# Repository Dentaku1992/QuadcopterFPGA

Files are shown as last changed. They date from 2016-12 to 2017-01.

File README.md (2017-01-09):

#Design of a quadcopter controller in VHDL

###Overview

In this project, a quad copter flight controller was designed in 'pure' hardware making use of a FPGA (Mojo development board). A PID control unit was used in order to provide stabilization around the three axes of movement of the quad copter. Due to the limited resources that are available on the FPGA (Spartan 6 SLX9), different approaches are used to fit the PID controllers into the FPGA. It was investigated whether there can be made use of the high-speed DSP48 slices available in the Spartan 6 or the Xilinx IP Core multiplier. In order to achieve a minimal resource design, the different channels of the FPGA were multiplexed.

In addition to the design of a PID controller, various other system components were designed as well. 
	
- A PWM generator to control the BLDC engines.
- A mixing unit, to generate the correct control signal for each engine.
- An SPI slave interface to communicate with different sensors and make it possible to access the quadcopter's register.
- A PWM reader in order to read the incomming signal from te remote control.

All hardware was simulated and then tested on an FPGA. Using Matlab and Simulink the necessary calculations and simulations are made before the VHDL implementation was done. In addition to the hardware, the quadcopterframe is fully designed as well. This frame is designed in such a way that it consists of several parts which can be manufactured by a 3D printer.

###Author

Gert-Jan Andries - http://www.gertjanandries.com - info@gertjanandries.com

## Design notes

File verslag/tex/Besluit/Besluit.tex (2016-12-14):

\chapter{Besluit}
\label{besluit}

	\par Het project heeft een zeer grote omvang en kon tijdens de duurtijd van het projectlab niet volledig voltooid worden. Een overzicht van welke items voltooid werden en welke niet, is weergegeven in figuur \ref{quad_ready}.

	\begin{figure}[H]					  
		  \centering
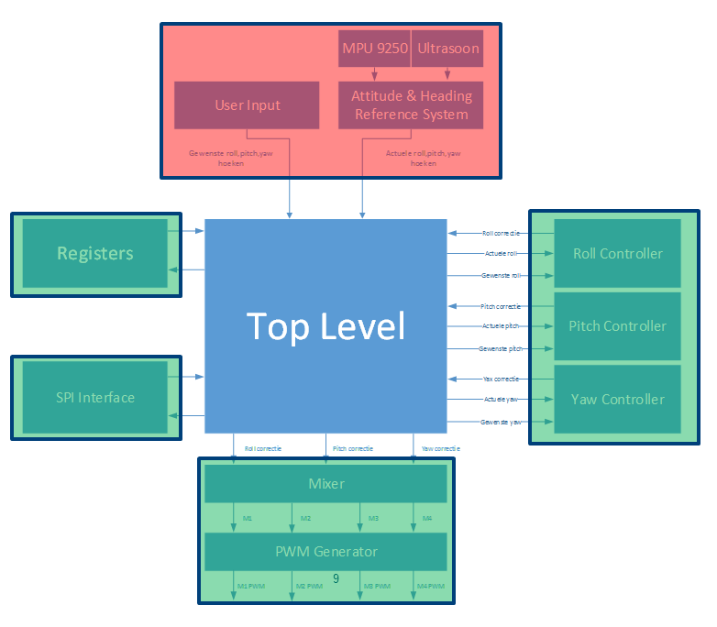
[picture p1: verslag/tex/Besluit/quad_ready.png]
		  
		  \caption{Overzicht van de projectstatus}
		  \label{quad_ready}
	\end{figure}

	\par De PID controller is volledig ge\"implementeerd  en geoptimaliseerd naar resources zodat deze past in de Spartan 6 FPGA. Hierbij werden verschillende iteraties doorlopen die telkens een andere methodiek gebruikten. Aan de hand van Simulink en testbenches werd de werking van de PID controller gevalideerd. De PID controller kon omwille van het ontbreken van sensordata nog niet getest worden op de FPGA zelf. Wel werd al een synthese uitgevoerd om na te gaan of de verschillende PID controllers pasten in het FPGA ontwerp. 

	\par De SPI slave interface werd ontwikkeld aan de hand van dezelfde parameters als het Mojo board gebruikt om te communiceren met de analoge inputs. Op deze manier kan de SPI interface veelzijdig ingezet worden. Via een testbench werd de werking gevalideerd alvorens de interface uit te testen op een FPGA. Wanneer de testbench het gewenste resultaat gaf, werd een test uitgevoerd op de FPGA zelf. Ook hier was de werking perfect en kwamen geen problemen aan het licht.

	\par De PWM generator en motormixer zijn volledig ge\"implementeerd in VHDL. De werking van de PWM generator is reeds getest op een FPGA door het aansturen van de vier verschillende motoren. Hierbij werd ook gebruik gemaakt van de SPI interface om de gewenste PWM instelling te maken. Alles werkt naar behoren. Er dient wel rekening gehouden te worden dat bij het aanleggen van het systeem een vaste PWM waarde aan de motoren wordt aangelegd om deze te activeren. Na ongeveer 1 \'a 2 seconden (beepgeluid bij de motor) zijn de motoren actief en kunnen ze gebruikt worden.

	\par Het quadcopterframe is vollledig geprint, maar dient nog geassambleerd te worden. Door de relatief lange printtijd was er onvoldoende tijd om deze assemblage uit te voeren gedurende het projectlab. De laatste prints waren helaas pas de dag zelf klaar.

	\par Het globale autopilot systeem kon niet getest worden omdat nog niet alle componenten voltooid zijn. De delen die wel getest konden worden, zijn uitvoerig getest en gaven ook het verwachte resultaat.

	\par In het verdere verloop van het project dienen volgende taken nog uitgevoerd te worden.

		\begin{itemize}
			\item Assamblage van het frame.
			\item Alle systeemcomponenten met elkaar verbinden.
			\item Implementeren van AHRS door middel van SPI slave connectie.
			\item Alle data tussen de verschillende componenten in het juiste formaat omzetten.
			\item Bepalen van de K\textsubscript{p}, K\textsubscript{i} en K\textsubscript{d} parameters.
			\item Uitbreiden van de registers.
			\item Globale systeemtest.
		\end{itemize}

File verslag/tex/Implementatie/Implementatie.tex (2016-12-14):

\chapter{Implementatie}

	\par In dit hoofdstuk zal de implementatie van het volledige systeem besproken worden. Er zal vooral de nadruk gelegd worden op de moeilijkheden en problemen die zich voordeden tijdens het ontwikkelproces.

	\section{PID regelaar}

		\par De PID regelaar vormt het belangrijkste onderdeel van de quadcoptersturing. Deze component zal per as ge\"implementeerd moeten worden. Daarnaast kan de PID in een verder stadia ook gebruikt worden om de hoogte te stabiliseren. Er dient dus een flexibele component ontworpen te worden die meerdere malen ingezet kan worden. Hierbij is het belangrijk dat de waarden voor K\textsubscript{p}, K\textsubscript{i} en K\textsubscript{d} per controller ingesteld kunnen worden. Daarnaast is het ook mooi meegenomen om deze real-time aanpasbaar te maken. 

		\par De PID controller werd ontwikkeld in drie iteraties. Vanwege de hardware beperkingen van de FPGA was het nodig om een volledig re-design uit te voeren van de component. Deze stappen zullen hieronder verder toegelicht worden.

		\subsection{PID controller door middel van DSP48A slices}

			\par Vanuit theoretisch oogpunt zijn DSP48 slices ideaal voor het implementeren van een PID regelaar. De bewerkingen die uitgevoerd dienen te worden beperken zich tot optellen en vermenigvuldigen (MAC). Op deze manier wordt een hoge snelheid van de component mogelijk. Per PID regelaar zijn vier DSP48 slices nodig. In figuur \ref{pid_dsp48} is de onderverdeling weergegeven van DSP48 slices binnen de PID regelaar. Hierbij zijn de functies van slice 2 en 3 exact hetzelfde. Bij de laatste DSP48 slice is een terugkoppeling voorzien. Om ervoor te zorgen dat het resultaat nooit overflowt, dient er een downscaling te gebeuren bij de terugkoppeling. Deze wordt in \textquotesingle gewone\textquotesingle   logica uitgevoerd en zal het proces vertragen. Door het introduceren van de nodige \textquotesingle pipes\textquotesingle  wordt de maximale snelheid van implementatie bereikt.
				
				\begin{figure}[H]					  
					  \centering
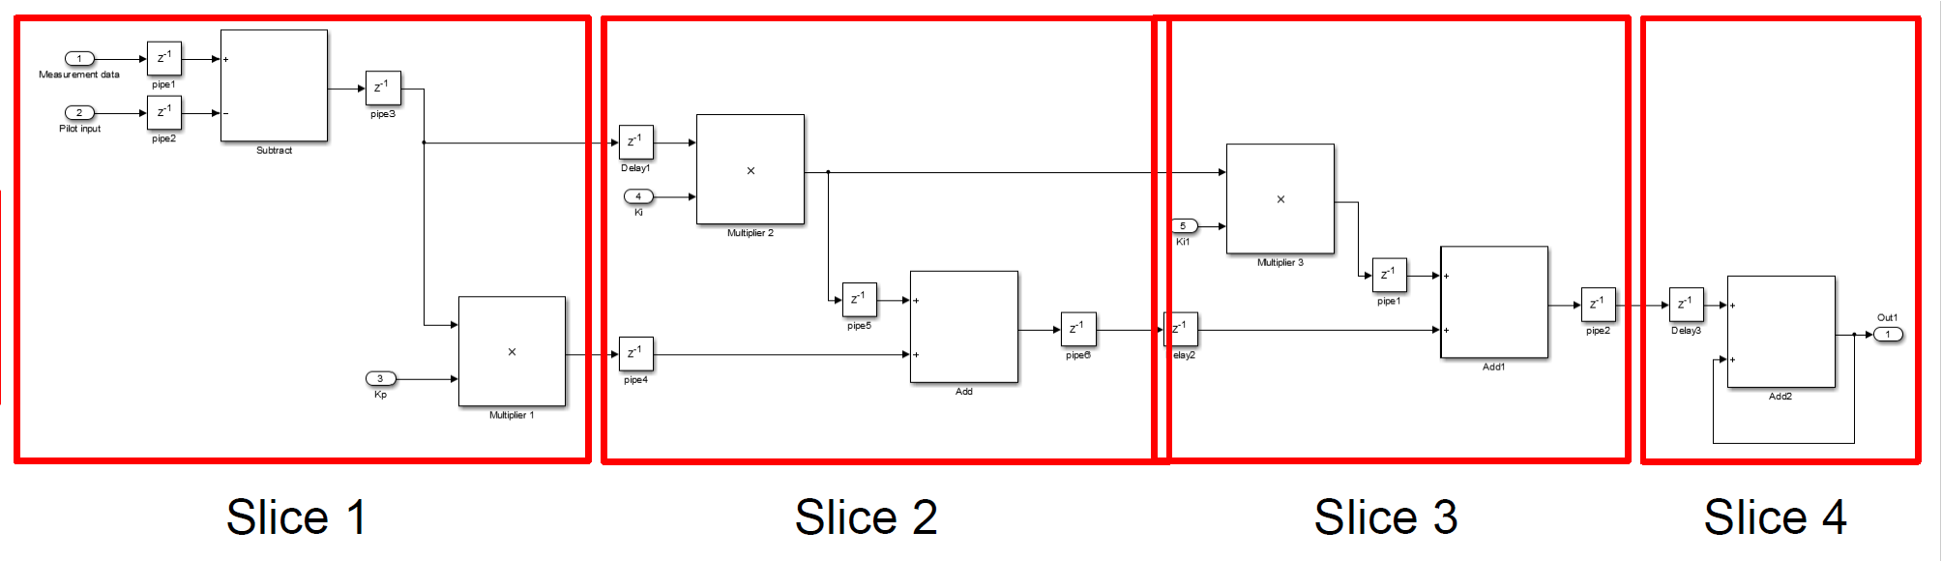
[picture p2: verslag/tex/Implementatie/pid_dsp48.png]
					  
					  \caption{Overzicht van een PID controller op basis van DSP48 slices}
					  \label{pid_dsp48}
				\end{figure}

			\par Bovenstaande code werd in een eerste fase ge\"implementeerd door middel van de Xilinx System Generator. Wanneer de VHDL code gegenereerd diende te worden, doken er steeds fouten op. Opzoekwerk heeft uitgewezen dat de System Generator niet compatibel is met Windows 8. Een Windows 7 apparaat met alle nodige software en licenties was helaas niet beschikbaar. Er werd overgegaan naar het implementeren van de PID in Xilinx ISE. Hierbij werd gebruik gemaakt van de IP Coregen voor het genereren van de juiste instellingen binnen de DSP48 slices.

			\par Door eerste synthese resultaten bleek dat het niet mogelijk was om drie of vier PID's te implementeren op de Spartan 6 FPGA wegens gebrek aan resources. Een mogelijke oplossing was het multiplexen van de PID regeling. Op die manier is er slechts \'e\'en PID regelaar nodig die afwisselend de berekeningen uitvoert voor een bepaald kanaal. De implementatie hiervan bleek echter te complex om te realiseren omdat de PID steeds de vorige resultaten nodig heeft om het volgende te berekenen. Deze data zou dus moeten opgeslagen worden. Daarnaast was het ook niet steeds mogelijk om deze waarden terug op de juiste plaats in het DSP48 slice te laden vanwege de beperkingen van ingangssignalen.

			\par Er dient dus een andere oplossing gevonden te worden om de PID in de Spartan 6 FPGA te implementeren.

		\subsection{PID controller door middel van IPCore multiplier}
		\label{pid_mult}

			\par Een tweede aanpak was om de PID te implementeren aan de hand van \textquotesingle gewone\textquotesingle  logica. Om de vermenigvuldigingen uit te voeren wordt gebruik gemaakt van de IP Core multiplier. Er zijn dus drie van deze multipliers nodig om de volledige component te realiseren. 

			\par Bij het aanmaken van deze multipliers zijn verschillende keuzes mogelijk. Er kan gekozen worden tussen een implementatie die gebruik maakt van ExtremeDSP (DSP48A slices) of een implementatie die gebruik maakt van LUT's en FF. Afhankelijk van de gekozen optie zullen de timings verschillen. Er is ook een mogelijk om te optimaliseren naar area (minimaal gebruik aan resources) of naar snelheid. Er werd gekozen om te minimaliseren naar area. Hierbij maakte de multiplier enkel gebruik van LUT's en FF. 

			\par Via Xilinx Vivado werd een eerste versie van deze PID ge\"implementeerd en gesimuleerd. De keuze voor Vivado werd gemaakt omwille van problemen met de ISE simulator op Windows 8. Daarnaast was het ook niet mogelijk om CoreIP componenten te simuleren in Modelsim vanwege een probleem met de bibliotheken. Xilinx biedt deze niet meer aan, omdat zij een eigen simulator ontwikkeld hebben.

			\par De simulaties leverden dezelfde resultaten op als bekomen in Simulink. Er kon dus besloten worden dat de implementatie van de PID gelijkaardig is als de versie in Simulink. Bij het verder onderzoeken van de synthese resultaten bleek dat er op het eerste zicht voldoende resources beschikbaar waren om vier PID controllers te implementeren. Omdat er niet enkel een PID op de FPGA ge\"implementeerd moet worden, maar ook nog een reeks andere componenten zou het toch kunnen dat men niet voldoende resources ter beschikking heeft.

			\par  Er dient dus een andere oplossing gevonden te worden om de PID in de Spartan 6 FPGA te implementeren met een minimaal gebruik aan resources.

		\subsection{PID controller door middel van multiplexed IPCore multiplier}			

			\par Een oplossing om de resources binnen een PID controller aanzienlijk te beperken is door in plaats van drie multipliers slechts \'e\'en multiplier te gebruiken. Hierbij zal telkens de P, I en D actie uitgevoerd worden. De snelheid van het component zal hierdoor dalen met ongeveer een facor drie, maar dit zal weinig invloed hebben op de werking van de autopilot. Aangezien de sensordata binnenkomt met een snelheid van enkele kHz en de PID component geklokt kan worden aan een snelheid van enkele MHz zal hier geen effect van opgemerkt kunnen worden.

			\par De implementatie gebeurt door middel van een state machine. In een eerste state zullen de  K\textsubscript{p}, K\textsubscript{i} en K\textsubscript{d} waarden ingelezen worden. Op deze manier zijn ze per berekening real-time aanpasbaar. In de volgende states zullen de P, I en D acties uitgevoerd worden. Dit houdt in dat de data die aan de multiplier aangelegd wordt, wijzigt per state. In de laatste state wordt een vlag kort hoog geplaatst om aan te geven dat de berekening klaar is. Er is dus maar \'e\'en multiplier nodig die gemultiplext wordt.

			\par Door het beperken van het aantal multipliers kon de snelheid van de multiplier geoptimaliseerd worden door toch gebruik te maken van DSP48 slices binnen deze multiplier. Deze wijziging werd dan ook doorgevoerd in de component.
\newpage
			\par Simulaties van de bovenstaande PID leverden exact hetzelfde resultaat op als de PID beschreven in paragraaf \ref{pid_mult}. Een overzicht van deze testbench is weergegeven in figuur \ref{pid_tb_mult}.

				\begin{figure}[H]					  
					  \centering
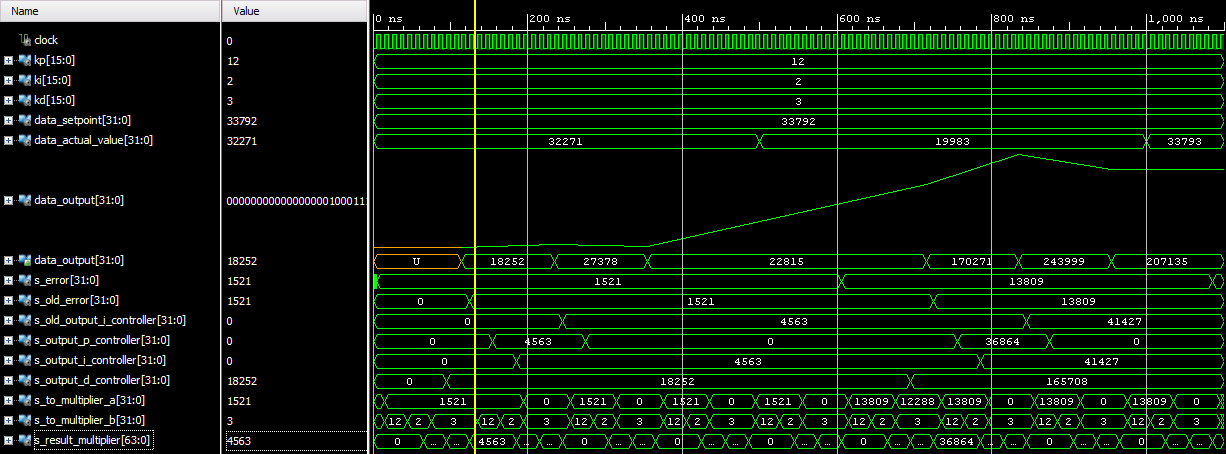
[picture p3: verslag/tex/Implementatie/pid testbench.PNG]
					  
					  \caption{Simulatieresultaat van PID regelaar met gemultiplext multiplier}
					  \label{pid_tb_mult}
				\end{figure}

			\par Wanneer men figuur \ref{pid_tb_mult} nader bekijkt, kan men opmerken dat wanneer de wenswaarde bereikt is, en bijgevolg het errorsignaal 0 is, de uitvoer niet terugvalt naar 0. De reden hiervoor is eenvoudig te verklaren. Aangezien de testbench werkt door middel van het aanleggen van bepaalde signalen voor gemeten waarde op bepaalde tijdstippen, heeft men hier niet te maken met een echt systeem. De I actie van de PID wordt berekend door middel van volgende formule.

				\[ I\textsubscript{regelaar} = (Error \cdot K\textsubscript{i} + Old_K\textsubscript{i} ) \] 

			\par Er wordt dus steeds een berekening gemaakt op basis van de oude waarde van K\textsubscript{i} waardoor de waarde nooit 0 wordt in de simulatie. In een echt systeem wordt dit probleem onmiddellijk opgelost omdat de regelaar zal blijven bijregelen. De sensor zal opmerken dat de waarde de wens overstijgt en een tegenactie ondernemen. 

		\subsection{Samenvattig PID controller}

			\par In listing \ref{PID_list_1} is de componentdefinitie van de PID controller weergegeven. Als invoer zijn zowel de sensordata als de gewenste waarde nodig. Daarnaast moeten ook de co\"effici\"enten voor  K\textsubscript{p}, K\textsubscript{i} en K\textsubscript{d} aangelegd worden. Deze co\"effici\"enten zijn real-time aanpasbaar.
\newpage
			\par Door de PID regelaar in verschillende stappen te ontwerpen konden steeds resources bespaard worden. Dit ging wel steeds ten koste van de snelheid van de component. Hoge snelheid bij deze component is niet zo belangrijk vanwege de relatief trage snelheid weermee de invoerdata kan aangeleverd worden. 

				\lstinputlisting[style=vhdl, caption=Overzicht van de PID component, label=PID_list_1]{Implementatie/pid.vhd}

	\section{PWM generator}

		\par Per motor is er telkens \'e\'en PWM generator nodig bij de quadcopter. De PWM generator zal een PWM signaal genereren op basis van een invoerwaarde die afkomstig is van de motormixing component. Om flexibiliteit te garanderen is de component volledig generiek gemaakt. Op deze manier kan zowel de resolutie als PWM frequentie gewijzigd worden. Een overzicht van de PWM component is weergegeven in listing \ref{pwm_gen}. 

			\lstinputlisting[style=vhdl, caption=Overzicht van de PWM component, label=pwm_gen]{Implementatie/pwm_gen.vhd}

	\section{Motor Mixing}

		\par Het motormixing gedeelte van de quadcopter is verantwoordelijk voor het genereren van de signalen die naar elke motor gestuurd moeten worden. Bij de opbouw van de quadcopter werd gekozen voor de \textquotesingle +\textquotesingle  configuraties. Het mixen van de motors gebeurt dan via het volgend algoritme.

			\[ Motor\textsubscript{front} = baseSnelheid + pitchOutput - yawOutput \]
			\[ Motor\textsubscript{left} = baseSnelheid + rollOutput + yawOutput \]
			\[ Motor\textsubscript{back} = baseSnelheid - pitchOutput - yawOutput \]
			\[ Motor\textsubscript{right} = baseSnelheid - rollOutput + yawOutput \]

		\par Hierbij is de baseSnelheid gelijk aan de idle snelheid van de motor vermeerderd met de throttle.

		\par Net als bij de PWM generator is ook deze component volledig generiek opgebouwd zodat deze makkelijk kan aangepast worden. Een overzicht van deze component is weergegeven in listing \ref{motormixing}.

			\lstinputlisting[style=vhdl, caption=Overzicht van de motormixing component, label=motormixing]{Implementatie/motormixing.vhd}

		\par Er zal ook rekening gehouden worden met de maxima waarde van het systeem. Wanneer een bepaalde waarde het maximum overschrijdt zal deze waarde automatisch worden teruggebracht naar de maximum waarde. De corrigerende actie zal daarom wat minder zijn dan gevraagd, maar de quadcopter blijft op deze manier wel binnen zijn limieten.

	\section{SPI slave interface}

		\par Zoals reeds eerder vermeld werd, voorziet de SPI interface de mogelijkheid om de autopilot te laten communiceren met de buitenwereld. In het vooronderzoek werd reeds de werking van een SPI slave interface aangehaald. Deze is in VHDL ge\"implementeerd voor CPOL en CPHA waarbij beiden gelijk zijn aan 0. Als databreedte werd gekozen voor 8 bits, ofwel 1 byte.

		%\par Via de SPI slave interface is het ook mogelijk om toegang te krijgen tot de analoge pinnen van het Mojo board. Dit kan in het verdere verloop van het project nodig zijn. 

		\par In  listing \ref{spi_slave} is een overzicht weergegeven van het SPI slave component. Er kan data ingevoerd worden die verstuurd moet worden. Daarnaast wordt er ook kort een vlag hoog geplaatst wanneer de data ontvangen is.

			\lstinputlisting[style=vhdl, caption=Overzicht van de SPI slave component, label=spi_slave]{Implementatie/spi_slave.vhd}

		\par Om de werking van deze component te valideren, is er een testbench voor deze component ontworpen. Deze wordt geanalyseerd alvorens de code te testen op het Mojo board. Het resultaat van deze testbench is weergegeven in figuur \ref{spi_slave_tb}.

				\begin{figure}[H]					  
					  \centering
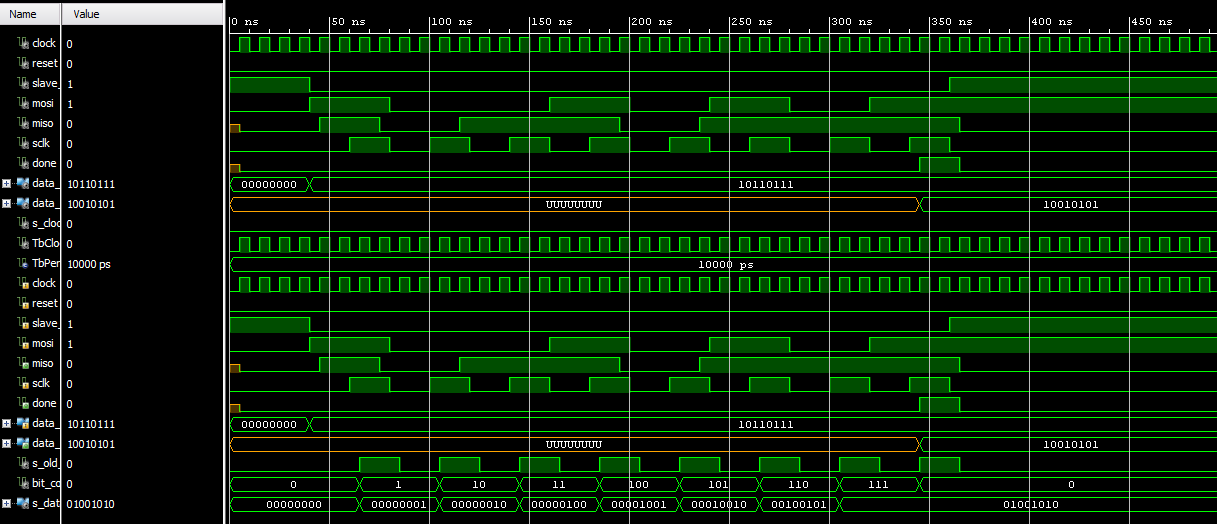
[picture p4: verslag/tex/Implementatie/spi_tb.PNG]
					  
					  \caption{Simulatieresultaat van SPI slave interface}
					  \label{spi_slave_tb}
				\end{figure}

	\section{Top level}

		\par Het toplevel verbindt alle systeemcomponenten met elkaar. Daarnaast is ook op dit niveau de register ge\"implementeerd aan de hand van de IP Coregen. Er wordt gebruik gemaakt van een block memory met 255 registers die elk een grootte hebben van 1 byte. Via de SPI interface kunnen deze registers zowel gelezen als ingesteld worden.

		\par Het toplevel zal ook de nodige signalen naar de buitenwereld brengen. Zo worden de signalen naar de motoren, SPI-apparaten en sensoren naar buiten gebracht. 

		\par Via de IP Core clocking wizard worden de verschillende klokken aangemaakt waarmee de componenten werken. 

	\section{Quadcopter Frame}

		\par Niet alleen de hardware componenten werden ontwikkeld tijdens dit projectlab, ook de quadcopter zelf werd ontworpen. Hierbij wordt gebruik gemaakt van een 3D printer die de verschillende onderdelen zal vervaardigen. In het computerprogramma Inventor worden alle onderdelen getekend en klaargemaakt om te kunnen worden geprint.

		\par Een quadcopter is opgebouwd uit vier armen die gepositioneerd zijn in een \textquotesingle x\textquotesingle. Zo\textquotesingle n arm is weergegeven in figuur \ref{quad_frame_pict}. 

			\begin{figure}[H]					  
				  \centering
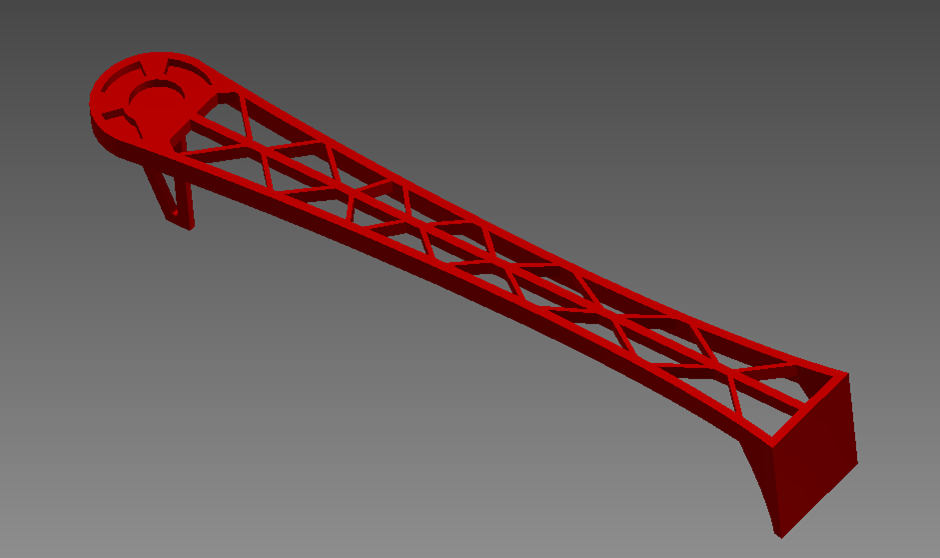
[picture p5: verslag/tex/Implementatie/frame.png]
				  
				  \caption{Weergave van een quadcopter arm}
				  \label{quad_frame_pict}
			\end{figure}

		\par De frameonderdelen werden vervaardigd door middel van een Ultimaker 3D printer. Indien er tijdens de vlucht een bepaald onderdeel beschadigd raakt, kan dit makkelijk opnieuw geprint worden en is quadcopter snel weer operatief. Het printen van een arm neemt ongeveer 4 uur in beslag.

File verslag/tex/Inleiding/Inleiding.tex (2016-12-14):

\chapter{Inleiding}
	
	\par In dit verslag worden de resultaten van het projectlab toegelicht. Elke stap die werd genomen om het eindresultaat te bekomen wordt kort besproken, alsook de moeilijkheden die zich hebben voorgedaan tijdens de ontwikkeling. Tenslotte wordt ook een besluit gevormd over het gehele project en worden de toekomstmogelijkheden kort toegelicht. 

	\section{Omschrijving van de opdracht}

		\par Het project is onderverdeeld in twee grote onderdelen. Enerzijds is er het stabilisatiealgoritme voor de quadcopter en anderzijds is er de sturing, hardware design en optical flowintegratie. De focus van het project zal gelegd worden op de stabiliteitsnelheid van het eindresultaat. Het onderdeel met het stabilisatie-algoritme omvat het genereren van PWM signalen die de motoren aansturen. Hiervoor is sensordata nodig van bijvoorbeeld een gyroscoop, accelerometer, magnetometer en barometer. Om de ruis uit deze metingen weg te filteren zal gebruik gemaakt worden van een filter, bijvoorbeeld Kalman, die ook in de FPGA zal ge\"integreerd worden. Naast data van sensoren zal de FPGA ook informatie ontvangen van een extra processor. Op deze extra processor wordt de communicatie met de grond voorzien (besturing), alsook een optical flow algoritme. 

		\par De stabilisatie zelf zal uitgevoerd worden door een PID of SM (sliding mode) dat ook op de FPGA zal ge\"integreerd worden. De instellingen van het stabilisatie-algoritme zullen gemaakt worden door middel van registers die door de externe processor kunnen ingesteld worden via I\textsuperscript{2}C of SPI. Via deze registers kan ook de actuele sensor- en systeeminformatie opgevraagd worden. De hardware bestaat uit een zelf te ontwikkelen printplaat gebaseerd op een FPGA (Spartan 6) die de stabilisatie en verwerking van de inputs verzorgt. Daarnaast bevat het ook een microcontroller die de communicatie voorziet, alsook de beeldverwerking voor de optical flow en het batterijbeheer. De communicatie zou verlopen volgens het MAVLink protocol, een gestandaardiseerd protocol dat communicatie voorziet onafhankelijk van de fysische laag waarop dit gebeurt. Een keuze voor het beste kanaal maakt ook deel uit van dit project. 
\newpage
		\par Optical flow detectie voorziet de  mogelijkheid om de horizontale ongewenste bewegingen tegen te werken en dus de quadcopter op een vaste positie te houden. De sturing voor de BLDC motoren wordt zelf ge\"implementeerd en vindt plaats op externe processoren die elk instaan voor \'e\'en enkele motor. Het FPGA ontwikkelbord waarmee gewerkt zal worden is het Mojo bord met een Spartan 6 processor. Dit bord zal zelf aangekocht worden. Verder zal ook een MPU9250 gebruikt worden om accelero-, magneto- en gyro-data te verzamelen. De andere sensoren die gebruikt zullen worden dienen te worden bepaald tijdens de looptijd van het project. 

		\par Wanneer alle sensoren getest zijn, worden ze samen met de FPGA (niet het ontwikkelbord) op de zelf ontworpen printplaat geplaatst om zo een quadcoptersturing te verkrijgen die onafhankelijk is van een ontwikkelbord of opgelegde pinout. Deze wordt gemonteerd op de quadcopter structuur die gemaakt zal worden door middel van een 3D printer. Dit maakt het nadien ook mogelijk om bij een crash een bepaald onderdeel snel te reproduceren.

		\par Dit projectlab kan worden opgesplitst in verschillende milestones.
			
		\begin{itemize}
			\item  Stabilisatie en sturing (Gert-Jan)
				\begin{itemize}
					\item Uitlezen sensoren
					\item Uitfilteren van ruis op sensordata
					\item Stabilisatie-algoritme PID/SM
					\item Instellingsmogelijkheid van registers
					\item Ontwerp van quadcopterframe
				\end{itemize}
			\item  Hardware en optical flow (Nick)
				\begin{itemize}
					\item Ontwerpen printplaat
					\item Implementeren MAVLink
					\item Selecteren communicatiekanaal
					\item Optical flow
					\item BLDC motor sturing
					\item Return to home functie
				\end{itemize}
		\end{itemize}
\newpage
	\section{Planning en werkwijze}

		\par De algemene werkwijze van het project kan onderverdeeld worden in vier grote blokken.

			\begin{description}
				
				\item[Onderzoek:] In deze fase van het project wordt een onderzoek uitgevoerd met betrekking tot quadcopters. Er wordt gekeken naar hoe een quadcopter bestuurd wordt en via welke algoritmen dit kan gebeuren. Daarnaast zal ook een studie gemaakt worden naar het implementeren van een PID-controller in een FPGA. Via simulaties in het programma simulink kunnen de algoritmen ge\"evalueerd worden.

				\item[Implementatie:] In deze fase worden de onderzoeksresultaten omgezet in code. Via het programma Xilinx ISE en Vivado wordt de implementatie voorzien op een FPGA. Aan de hand van het programma Modelsim worden de hardwaredesigns ge\"evalueerd alvorens deze op de FPGA worden getest.

				\item[Testen:] Wanneer de hardware gevalideerd is door middel van een testbench, kan deze getest worden op de FPGA zelf. Blok per blok zullen de nodige testen uitgevoerd worden en bijgestuurd waar nodig. 

				\item[Reflectie:] Elk ontworpen blok zal onderworpen worden aan een kritische evaluatie. Hierbij wordt gekeken naar performantie, accuraatheid en werking binnen het geheel. Waar nodig wordt bijgestuurd. Regelmatige communicatie met medestudent Nick, die de hardware (PCB) ontwerpt is hierbij nodig.

			\end{description}

		\par Een beknopte projectplanning wordt hieronder weergegeven. Een uitgebreide versie hiervan is terug te vinden in appendix \ref{app:A} op pagina \pageref{app:A}. Deze uitgebreide versie houdt rekening met de initi\"ele planning. Hieronder is het werkelijke verloop van het project weergegeven.

			\begin{itemize}
				
				\item[Week 1:] 
					\begin{itemize}
						\item Keuze maken van het project uit de aangeboden projecten.  
						\item Registreren van het gekozen project.
					\end{itemize}

				\item[Week 2:] 
					\begin{itemize}
						\item Indienen van de projectplanning.
						\item Onderzoek naar quadcopters en besturing.
						\item Studie PID en digitalisering.
						\item Studie IMU sensoren.
					\end{itemize}

				\item[Week 3:]
					\begin{itemize}
						\item Simulatie van PID algoritme in Matlab en Simulink.
						\item Theoretisch ontwerp van PID door middel van DSP48 slices.
						\item Kennismaking Mojo ontwikelbord en Xilinx ISE.
					\end{itemize}				

				\item[Week 4:]
					\begin{itemize}
						\item Tussentijdse presentatie van het project.
						\item Implementatie van PID door middel van DSP48 slices .
						\item Evaluatie van PID implementatie en bijsturing.
						\item Ontwerp van quadcopter frame in Inventor.
					\end{itemize}					

				\item[Week 5:]
					\begin{itemize}
						\item Ontwerp SPI slave interface in VHDL.
						\item Bijsturen PID ontwerp, implementatie met behulp van IP core multiplier.
						\item Validatie van ontwerp door middel van testbenches.

					\end{itemize}					

				\item[Week 6:]
					\begin{itemize}
						\item Bijsturen PID ontwerp, implementatie met behulp van IP core multiplier.
						\item Validatie van ontwerp door middel van testbenches.
						\item Ontwerp SPI slave interface aanpassen aan Mojo SPI.
						\item Testprint van quadcopter arm en stevigheidstest.
					\end{itemize}					

				\item[Week 7:]
					\begin{itemize}
						\item Bijsturen ontwerp van quadcopter arm.
						\item Printen van vier quadcopterarmen.
						\item Ontwerp van PWM generator in VHDL.
					\end{itemize}					

				\item[Week 8:]
					\begin{itemize}
						\item Tussentijdse presentatie van het project.
						\item Testen PWM generator op Mojo. 
						\item Testen van SPI slave interface op Mojo. 
						\item Ontwerp bijsturen waar nodig.
					\end{itemize}					

				\item[Week 9:]
					\begin{itemize}
						\item PID regeling aanpassen naar multiplexing om resources te besparen op de FPGA.
						\item Valideren van het nieuwe PID ontwerp.
						\item Testen van PWM en SPI samen op Mojo bord.
					\end{itemize}					

				\item[Week 10:]
					\begin{itemize}
						\item Ontwerpen van motormixingalgoritme in VHDL.
						\item Optimalisatie van PID controller.
						\item Implementatie van registers.
					\end{itemize}					

				\item[Week 11:]
					\begin{itemize}
						\item Labobad Gent.
					\end{itemize}					

				\item[Week 12:]
					\begin{itemize}
						\item Eindpresentatie en demo van het labproject.
					\end{itemize}								

				\item[Week 14:]
					\begin{itemize}
						\item Indienen van het eindverslag.
					\end{itemize}

			\end{itemize}

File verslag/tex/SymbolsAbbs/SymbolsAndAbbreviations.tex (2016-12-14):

% Een lijst van figuren en tabellen is optioneel
%\listoffigures
%\listoftables
% Bij een beperkt aantal figuren en tabellen gebruik je liever het volgende:
\listoffiguresandtables
% De lijst van symbolen is eveneens optioneel.
% Deze lijst moet wel manueel aangemaakt worden, bv. als volgt:
\chapter{Lijst van afkortingen}

\begin{flushleft}
  \renewcommand{\arraystretch}{1.1}
  \begin{tabularx}{\textwidth}{@{}p{12mm}X@{}}
			ADC 					& Analog to Digital Converter\\
			ARM 					& Advanced RISC Machines\\			
			AHRS					& Attitude and Heading Reference System\\
			BLDC					& Brushless DC\\
			CPHA					& Phase Polarity\\
			CPOL					& Clock Polarity\\
			DC						& Direct Current \\
			DMP						& Digital Motion Processing\\
			DSP 					& Digital Signal Processing\\		
			ESC						& Engine Speed Controller\\
			FPGA					& Field Programmable Gate Array 	\\
			I\textsuperscript{2}C 	& Inter-IC bus\\		
			IC 						& Integrated circuit\\		
			IMU						& Inertial Measurement Unit\\
			IO						& Input Output\\
			IP						& Intellectual Property\\
			KU 						& Katholieke Universiteit\\		
			KUL 					& Katholieke Universiteit Leuven\\		
			MAC 					& Multiply and Accumulate\\		
			MAVLink					& Micro Air Vehicle Communication Protocol	\\
			MHz 					& Megahertz\\		
			MISO					& Master In Slave Out\\
			MOSI					& Master Out Slave In\\
			PCB 					& Printed Circuit Board\\		
			PID						& Proportioneel Integrerend Differenti\"erend	\\
			PWM						& Pulse Width Modulation\\
			RF						& Radio Frequency\\
			SCLK					& Serial Clock Line\\
			SM						& Sliding Mode	\\
			SPI 					& Serial Peripheral Interface\\		
			SS 						& Slave Select\\
			UART 					& Universal Asynchronous Receiver Transmitter\\		
			USB						& Universal Serial Bus\\		
			VHDL					& Very High Speed Integrated Circuit Hardware Description Language\\

  \end{tabularx}
\end{flushleft}

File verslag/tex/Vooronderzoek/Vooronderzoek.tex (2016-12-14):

\chapter{Vooronderzoek}

	\par In dit hoofdstuk zullen de verschillende resultaten van het vooronderzoek besproken worden. Ook de simulaties in het programma simulink worden kort toegelicht. Op het einde van dit hoofdstuk wordt een compleet systeemoverzicht weergegeven. 

	\section{Quadcopters}

		\subsection{Wat is een quadcopter}
			
			\par Een quadcopter, ook wel quadrocopter genoemd, is een hefschroefvliegtuig dat, zoals de naam al doet vermoeden, aangedreven wordt door vier motoren. In tegenstelling tot een conventionele helikopter maakt een quadcopter gebruik van symmetrisch hellende propellors die in groepen van twee dezelfde draairichting hebben. Op deze manier wordt de tolbeweging die ontstaat door de krachtwerking van de motoren tegengewerkt en gereduceerd tot nul. Dit zorgt ervoor dat de quadcopter tijdens de vlucht niet rondtolt. Bij een klassieke helikopter wordt het opheffen van deze kracht voorzien door de staartrotor.

				\begin{figure}[H]					  
					  \centering
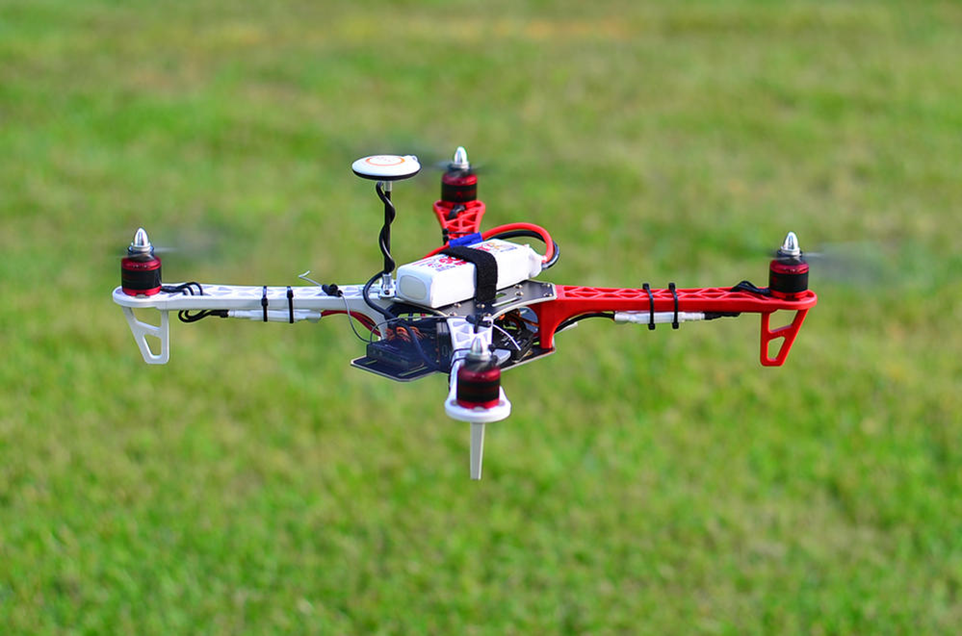
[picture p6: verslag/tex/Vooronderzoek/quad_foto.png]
					  
					  \caption{Quadcopter in actie}
					  \label{quadcopter_foto}
				\end{figure}

			\par Een quadcopter is opgebouwd uit een frame dat vier armen bevat. Op het uiteinde van deze armen zijn de motoren (brushless DC) bevestigd. Om de motoren aan te sturen wordt gebruik gemaakt van een \textquoteleft engine speed controller \textquoteright (ESC). Deze zorgt voor de aansturing van de motoren. Een centrale eenheid regelt zowel de stabilisatie als de invoer van de piloot.

			\par Een quadcopter is van nature onstabiel. Een regelsysteem dat stabilisatie voorziet tijdens de vlucht is nodig. Dit systeem zal ten minste een stabilisatie voorzien rond de roll-, pitch- en yaw-as. Optioneel kan ook een stabilisatie voor drift en hoogte voorzien worden. Deze stabilisatie wordt meestal voorzien door middel van een PID controller voor elke as.

			\par Naast het voorzien van stabilisatie dient er ook gereageerd te worden op de invoer van de piloot. De centrale eenheid (autopilot) implementeert typisch deze functies. Naast het voorzien van deze basisfuncties kunnen nog verschillende opties toegevoegd worden zoals een return-to-home functie, een autoland functie\ldots 

			\par Als basis voor deze autopilot wordt een IMU unit voorzien. Deze beschikt aan de hand van een accelerometer-, magnetometer- en gyroscoop-informatie over de actuele attitude van de quadcopter. Op basis van deze gegevens kan een stabilisatie uitgevoerd worden.

			\par Hiervoor zijn reeds verschillende systemen op de markt. Een populair systeem binnen de amateurpiloten is ArduPilot. Deze autopilot is volledig gebaseerd op Arduino en compatibel met zowat alle quadcopters en kleine vliegtuigen. 

			\par Net zoals ArduPilot zijn zowat alle autopilot systemen momenteel op de markt, gebaseerd op een microcontroller. Het doel van dit projectlab is het onderzoeken of de basisfuncties van een autopilot ook ge\"implementeerd kunnen worden op een FPGA.

		\subsection{Configuraties}

			\par Een quadcopter kan opgebouwd worden op twee verschillende manieren. Afhankelijk van hoe de armen aan het centrale stuk geplaatst worden, verkrijgt men ofwel een \textquoteleft+\textquoteright  ofwel een \textquoteleft x\textquoteright  configuratie. De configuratie wordt dus bepaald door de vliegrichting van de quadcopter ten opzichte van de propellers. In figuur \ref{quad_config} is een overzicht van beide configuraties weergegeven.

				\begin{figure}[H]					  
					  \centering
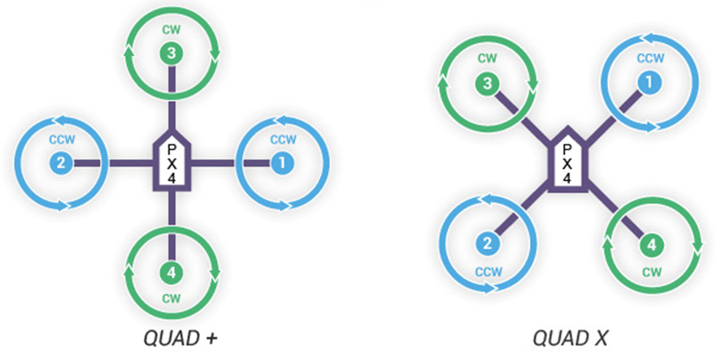
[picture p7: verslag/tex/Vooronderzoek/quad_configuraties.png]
					  
					  \caption{Verschillende configuratiemogelijkheden van een quadcopter}
					  \label{quad_config}
				\end{figure}

			\par De keuze van een bepaalde configuratie heeft een invloed op de manier van besturing, maar ook op het algoritme waarmee de verschillende motoren worden aangestuurd. Wanneer men gebruikt maakt van de  \textquoteleft x\textquoteright configuratie, zijn er twee motoren nodig om een beweging om een bepaalde as uit te voeren. 

			\par Het spreekt voor zich dat het algoritme dat nodig is om de motoren aan te sturen bij een  \textquoteleft x\textquoteright configuratie complexer is dan bij de keuze van een  \textquoteleft +\textquoteright configuratie. Er wordt dus gekozen voor de  \textquoteleft +\textquoteright configuratie binnen dit projectlab.

		\subsection{Besturing van een quadcopter}
			
			\par Om een quadcopter te besturen dienen de motoren op een correcte wijze aangestuurd te worden. Afhankelijk van hoe de motoren aangestuurd worden zal de quadcopter stijgen, dalen, gieren, of stampen. Daarnaast is het ook mogelijk een combinatie van de verschillende bewegingen samen uit te voeren.

			\par Om een quadcopter te laten stijgen of dalen, dienen de vier motoren gelijktijdig versneld of vertraagd te worden. 

			\par Om een quadcopter te laten bewegen om zijn verticale as moet de snelheid van twee motoren die \'e\'enzelfde draairichting hebben verhoogd worden. Hierdoor zal het koppel op de quadcopter toenemen waardoor een gierbeweging zal ontstaan.

			\par Om een quadcopter vooruit, achteruit, link of rechts te laten bewegen in de \textquoteleft + \textquoteright  configuratie volstaat het om \'e\'en motor sneller te laten bewegen dan de anderen. Hierdoor zal de quadcopter kantelen in een bepaalde richting, met een verplaatsing tot gevolg.

			\par In figuren \ref{quad_up_down}, \ref{quad_gieren} en \ref{quad_kantelen} is een overzicht weergegeven van de besturing van een quadcopter in de \textquoteleft + \textquoteright configuratie.

		\begin{figure}[H]
			\centering
				\begin{minipage}[b]{0.3\textwidth}
					\centering
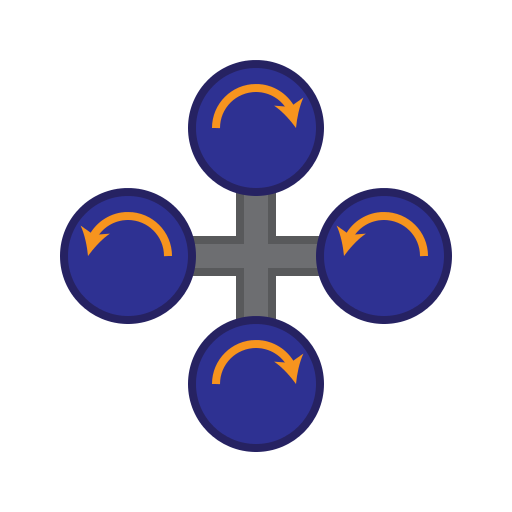
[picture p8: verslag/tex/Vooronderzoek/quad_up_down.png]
					
					\caption[Omhoog en omlaag]{Omhoog en omlaag}
					\label{quad_up_down}
				\end{minipage}
			\quad
				\begin{minipage}[b]{0.3\textwidth}
					\centering
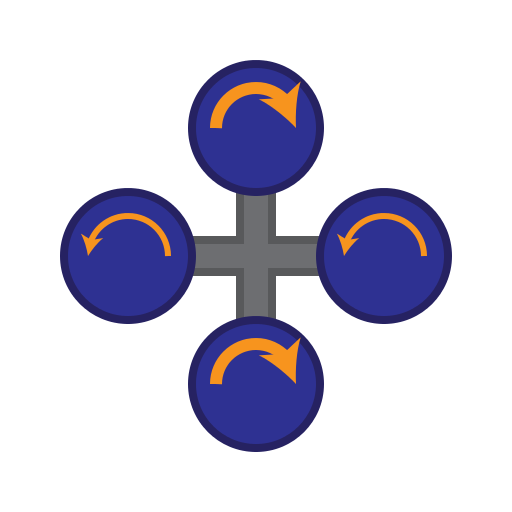
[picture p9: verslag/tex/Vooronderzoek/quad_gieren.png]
					
					\caption[Gieren]{Gieren \newline \ }
					\label{quad_gieren}
				\end{minipage}
			\quad
				\begin{minipage}[b]{0.3\textwidth}
					\centering
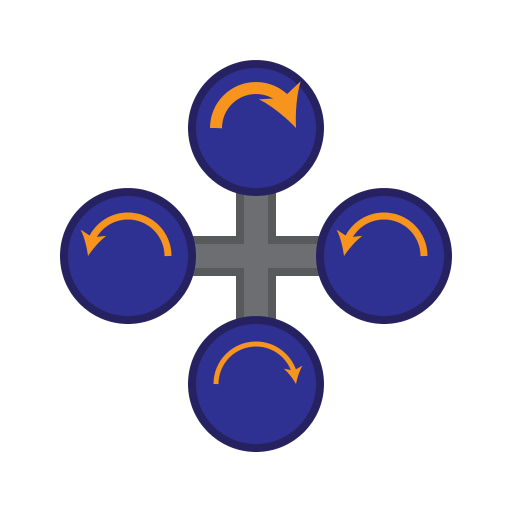
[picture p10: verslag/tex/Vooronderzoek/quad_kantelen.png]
					
					\caption[Kantelen]{Kantelen \newline \ }
					\label{quad_kantelen}
				\end{minipage}
		\end{figure}

	\section{PID regelaar}

		\par Een PID regelaar is een veel voorkomende regelaar binnen de procesregeling. De afkorting PID staat voor Proportioneel, Integrerend en Differenti\"erend. Dit zijn ook de acties waaruit de regelaar is opgebouwd.

		\subsection{Werkingsprincipe}

			\par De regeling gaat uit van het verschil tussen de gewenste waarde en de actuele gemeten waarde. Dit wordt omschreven als het foutsignaal. Het bijsturen van dit foutsignaal gebeurt in drie parallelle stappen.

				\begin{description}
					
					\item[P-actie:] De proportionele actie zal het foutsignaal versterken met een factor K\textsubscript{p}.

					\item[I-actie:] De integrerende actie zorgt voor een constante sommatie van het foutsignaal. Afhankelijk van hoe lang er een fout is tussen de gemeten en gewenste waarde, zal de integrerende actie meer of minder signaal uitsturen. De K\textsubscript{i} term, ook wel nasteltijd genoemd, bepaald het effect van deze actie. Hoe kleiner deze waarde, hoe krachtiger de actie.

					\item[D-actie:] De differenti\"erende actie zal reageren op de snelheid van verandering van het foutsignaal. Hoe hoger de factor K\textsubscript{d} wordt ingesteld, hoe sneller de wenswaarde bereikt zal worden.

				\end{description}

			\par Wiskundig kan men een PID regelaar als volgt omschrijven:

				\[ u(t) = K_{p}\cdot (e(t)+\frac{\int e(t)dt }{T_{i}}+ T_{d}\cdot \frac{de(t))}{dt}) \]

			\par Hierin is 

				\begin{conditions*}
					U(t)				& De uitgang van de regelaar				\\
					K\textsubscript{p}	& De proportionele actie van de regelaar	\\
					T\textsubscript{i}	& De integratietijd van de regelaar			\\
					T\textsubscript{d}	& De differentiatietijd van de regelaar 	\\
					E(t)				& Het errorsignaal							\\
				\end{conditions*}

			\par Het bepalen van de juiste constanten is een werk van trial-and-error. Dit zal dan ook experimenteel moeten vastgesteld worden op de quadcopter.

		\subsection{Digitalisatie van een PID}

			\par De formule die hierboven weergegeven is, kan als volgt vertaald worden naar een digitaal systeem.

				\[ U\textsubscript{k} = U\textsubscript{k-1} \cdot e\textsubscript{k} + b\textsubscript{0} \cdot + b\textsubscript{1} \cdot e\textsubscript{(k-1)} + b\textsubscript{2} \cdot e\textsubscript{(k-2)} \]

			\par Hierbij is

				\begin{itemize}
					\item[] $ b\textsubscript{0} = K\textsubscript{p}(1+ \frac{T\textsubscript{d}}{T}) $ \\					
					\item[] $ b\textsubscript{1} = K\textsubscript{i}(-1 +  \frac{T}{T\textsubscript{i}} -2\frac{T\textsubscript{d}}{T} ) $ \\		
					\item[] $ b\textsubscript{2} = K\textsubscript{d}(\frac{T\textsubscript{d}}{T}) $ \\
				\end{itemize}

			\par Deze formule kan weergegeven worden in het onderstaande schema.
	
				\begin{figure}[H]					  
					  \centering
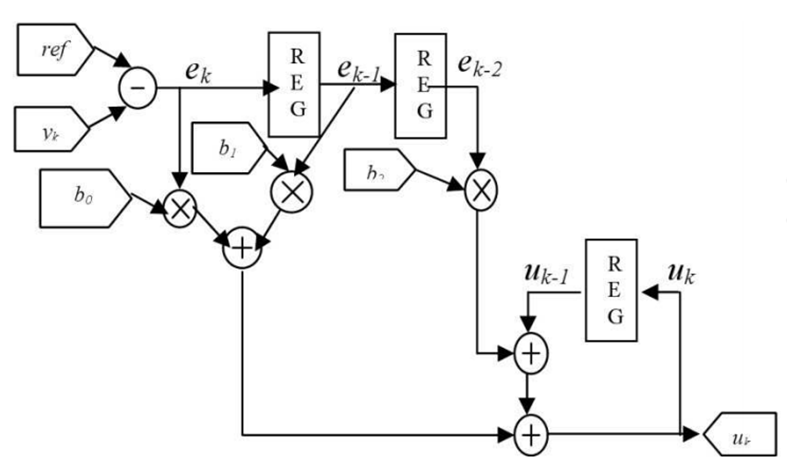
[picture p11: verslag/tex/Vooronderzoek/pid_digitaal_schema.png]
					  
					  \caption{Schematische voorstelling van een PID regelaar}
					  \label{pdi_digitaal_schema}
				\end{figure}

			\par De werking van de in figuur \ref{pdi_digitaal_schema} weergegeven regelaar wordt gevalideerd via het programma Simulink. Op deze manier kan reeds voor de FPGA implementatie gekeken worden of de regelaar zal doen wat er verwacht wordt. Daarnaast vormt deze simulatie een goede basis om het FPGA design te starten. In figuur \ref{pdi_simulink_schema} is de Simulink versie van de PID regelaar weergegeven.

				\begin{figure}[H]					  
					  \centering
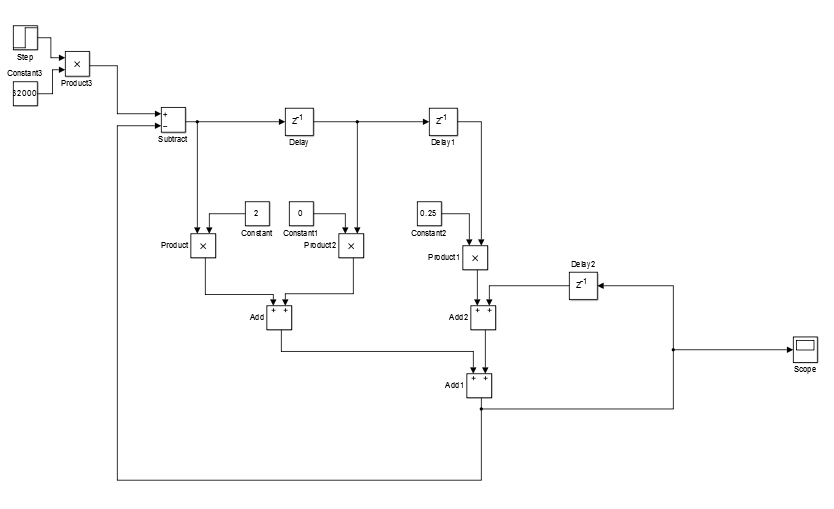
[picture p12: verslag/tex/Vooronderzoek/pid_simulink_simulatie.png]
					  
					  \caption{Simulink voorstelling van een PID regelaar}
					  \label{pdi_simulink_schema}
				\end{figure}

			\par Wanneer men de uitgang aan de ingang koppelt van bovenstaande PID wordt er aangenomen dat de nieuwe gemeten waarde gelijk is aan de uitgang van de PID. Dit levert het volgend resultaat op na simulatie.

				\begin{figure}[H]					  
					  \centering
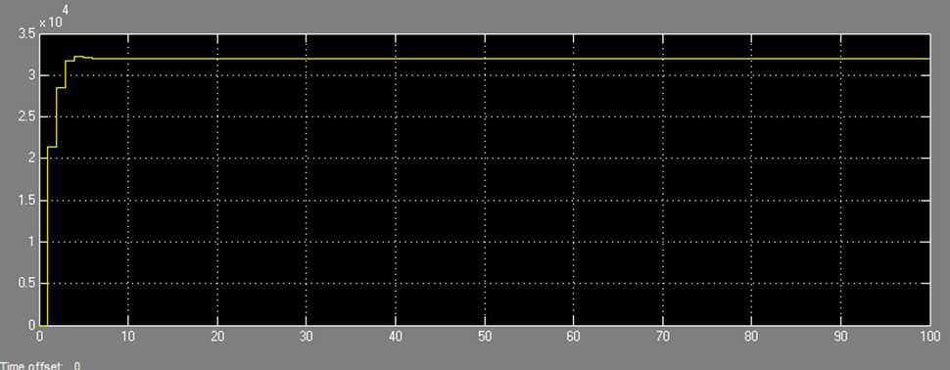
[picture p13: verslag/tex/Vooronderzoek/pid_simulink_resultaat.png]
					  
					  \caption{Resultaat van simulatie PID in Simulink }
					  \label{pdi_simulink_resultaat}
				\end{figure}

			\par In figuur \ref{pdi_simulink_resultaat} is duidelijk de werking van een PID waar te nemen. Het signaal klimt naar de gewenste waarde toe, maakt een kleine overshoot en stabiliseert vervolgens op het gewenste signaal. Dit is ook wat men verwacht van een PID. Men kan dus besluiten dat het schema in figuur \ref{pdi_digitaal_schema} voldoet aan de eisen en ge\"implementeerd kan worden in de FPGA.

	\section{Xilinx DSP48 slices}

		\par De Spartan 6 reeks bevat verschillende DSP48A slices. Deze MAC bouwstenen zijn door Xilinx speciaal ontworpen om DSP toepassingen te realiseren.

			\begin{figure}[H]					  
				  \centering
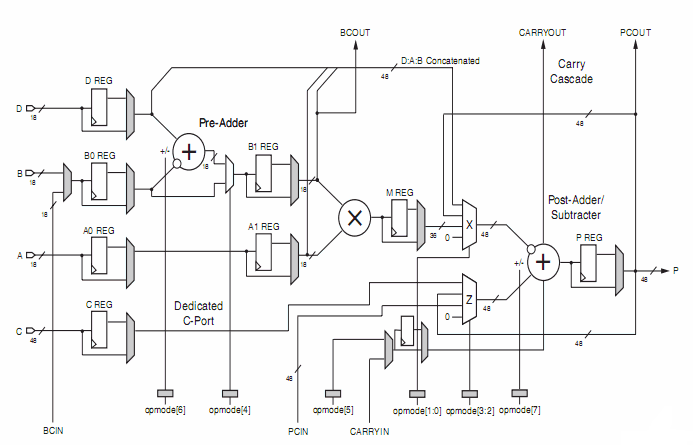
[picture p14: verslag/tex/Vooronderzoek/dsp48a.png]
				  
				  \caption{Interne structuur van een DSP48A slice }
				  \label{pdi_simulink_resultaat}
			\end{figure}

		\par Het doel van een DSP48 slice is het zo performant mogelijk uitvoeren van MAC operaties. Hiervoor zijn verschillende adders en een multiplier binnen het DSP48 slice aanwezig. Als invoer kan een signaal van maximaal 18 bits aangelegd worden. De uitgang is maximaal 48 bit. Hiervan is ook de naam DSP48 afgeleid.

		\par De DSP48A slices kunnen binnen de Xilinx ISE ontwikkelomgeving op verschillende manieren worden ge\"instantieerd. De eenvoudigste methode is via de IP Coregen. De gebruiker maakt stapsgewijs de instellingen op basis van een aantal selecties. Visueel wordt weergegeven welke instellingen gemaakt worden. Een andere manier om een DSP48 Slice te implementeren is door gebruik te maken van een zogenaamde Port Map in de code. Hierbij worden alle instellingen handmatig gemaakt en dient goed rekening gehouden te worden met de datasheet. Een derde manier om DSP48 slices te gebruiken is via de Xilinx System Generator. Dit is een pakket dat in samenwerking met Matlab en Simulink de mogelijkheid voorziet om visueel, door middel van blokken, een systeem samen te stellen en de nodige VHDL code te genereren. 

		\par De Spartan 6SLX9 beschikt over 12 DSP48A slices. Binnen het FPGA zullen deze gebruikt worden waar mogelijk om het gehele proces te versnellen.
\newpage
	\section{Mojo FPGA ontwikkelbord}

		\par Tijdens het projectlab zal gebruik gemaakt worden van het Mojo FPGA ontwikkelbord. Dit bord heeft een Spartan 6 XC6SLX9 FPGA aan boord waarbij de gebruiker beschikt over 84 digitale IO pinnen. Naast de digitale IO pinnen van het Mojo bord zijn er ook 8 analoge inputs voorzien. Deze bevinden zich op een externe ATmega controller die via een SPI interface communiceert met de FPGA.

		\par Het programmeren van het Mojo bord gebeurt op eenvoudige wijze. Via het programma Mojo loader kan een \texttt{.bit} bestand naar de externe ATmega geladen. Telkens wanneer de FPGA opgestart wordt zal het laatst opgeslagen \texttt{.bit} bestand geladen worden op de FPGA. Op deze manier dient na stroomuitval niet steeds opnieuw het \texttt{.bit} bestand geladen te worden.

		\par Er zijn reeds verschillende shields op de markt die het mogelijk maken om het Mojo board verder uit te breiden. Daarnaast is het project volledig open source waardoor er zelf ook makkelijk extra hardware ontwikkeld kan worden. Alle schema\textquotesingle s en PCB layouts zijn via de website van de makers vrij verkrijgbaar.

		\par In afbeelding \ref{mojo} is het Mojo bord weergegeven. Naast de 84 digitale en 8 analoge IO pinnen beschikt het Mojo bord ook over 8 leds die verbonden zijn met de FPGA.

			\begin{figure}[H]					  
				  \centering
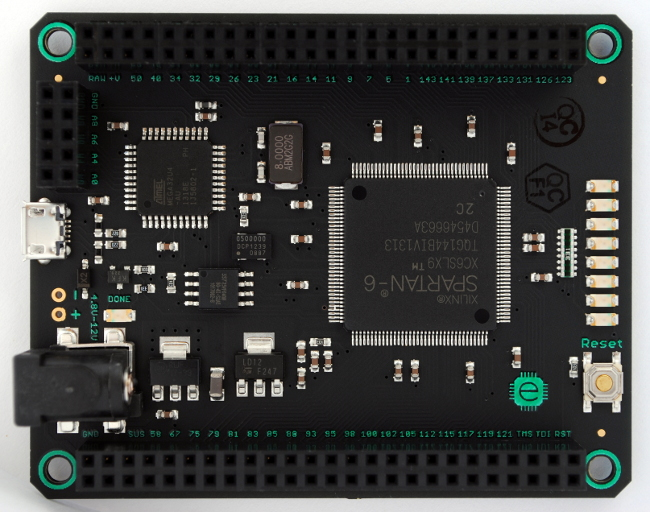
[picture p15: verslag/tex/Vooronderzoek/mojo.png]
				  
				  \caption{Overzicht van het Mojo FPGA ontwikkelbord}
				  \label{mojo}
			\end{figure}
\newpage
	\section{Sensoren}

		\par Om een stabilisatie te voorzien van de quadcopter is het noodzakelijk een inzicht te krijgen van zijn actuele attitude. Hiervoor wordt gebruik gemaakt van een IMU sensor. IMU staat voor inertial measurement unit. Deze unit bevat een combinatie van accelerometers, magnetometers en gyroscopen om zo informatie te verwerven over de huidige attitude van de quadcopter in de ruimte. Om daarbij ook informatie te verschaffen over de hoogte, wordt gebruik gemaakt van de combinatie van een ultrasone sensor en een barometer.

		\subsection{Opmeten van de attitude}

			\subsubsection{Principe}

			\par Een AHRS, attitude and heading reference system, voorziet de gebruiker van informatie over de stand van het vliegtuig. Om dit te berekenen wordt gebruik gemaakt van de data die afkomstig is van een IMU sensor. Zoals reeds hierboven beschreven werd, is een IMU sensor een combinatie van volgende drie sensoren.

				\begin{description}
				
					\item[Accelerometer:] Een accelerometer meet de versnelling van de quadcopter, vaak uitgedrukt in g-krachten. Aan de hand van deze versnelling kan bepaald worden of de quadcopter in een bepaalde richting beweegt of in vrije val is.
				
					\item[Gyroscoop:] Een gyroscoop meet de hoekverdraaiing op, uitgedrukt in radialen per seconde. Zo kan men de draairichting van de quadcopter bepalen. Deze hoekverdraaiing kan op zijn beurt gebruikt worden om de gemeten accelerometerwaarden te corrigeren. Indien de accelerometer namelijk niet in de correcte positie gehouden wordt, is het assenstelsel van de quadcopter verdraaid en zijn de gemeten x, y en z componenten niet correct ten opzichte van het assenstelsel in de re\"ele wereld.

					\item[Magnetometer:] Een magnetometer meet storingen in het aardmagnetisch veld op. Deze data wordt gebruikt om de performatie van de AHRS berekeningen op te voeren.
				
				\end{description}

			\par Aangezien men met de gyroscoop kan opmeten hoe groot de verdraaiing ten opzichte van het originele assenstelsel is, kunnen we het assenstelsel van de accelerometer corrigeren door matrixbewerkingen uit te voeren. Op die manier zijn de gemeten accelerometerwaarden toch te beschouwen vanuit het wereldse assenstelsel.

			\par Uit deze data wordt vervolgens de attitude van de quadcopter berekend. Deze bestaat uit de heading, de pitch-rate en de yaw-rate. 

			\par Vele sensoren gebruiken naast de boven beschreven parameters ook de temperatuur om een kalibratie uit te voeren en de nauwkeurigheid van het systeem te verbeteren.

			\par In figuur \ref{ahrs} is het principe van een AHRS op basis van IMU data weergegeven. 
			
			\begin{figure}[H]					  
				  \centering
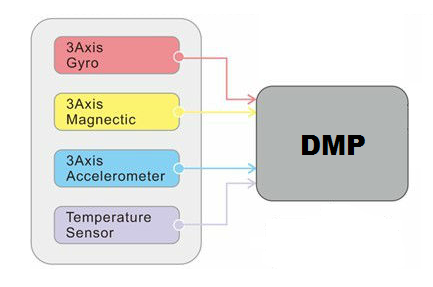
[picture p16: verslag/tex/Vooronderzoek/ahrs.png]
				  
				  \caption{Overzicht van een AHRS systeem}
				  \label{ahrs}
			\end{figure}

			\subsubsection{Sensoren}

				\par Vandaag de dag zijn er verschillende sensoren op de markt te verkrijgen. Onderzoek heeft uitgewezen dat binnen de UAV wereld de MPU reeks van InvenSense vaak gebruikt worden als IMU. Binnen deze reeks van sensoren komen twee sensoren in aanmerking.

					\begin{description}

						\item[MPU 6050:] Deze IMU omvat heel wat mogelijkheden. Zo is er een ingebouwde processor, de DMP (Digital Motion Processor), die reeds heel wat berekeningen op zich kan nemen. Deze DMP is in staat simpele gestures te detecteren, stappen te tellen, filtering uit te voeren van de sensorwaarden en meer aangezien deze volledig naar wens kan ingesteld worden. De nauwkeurigheid van deze IMU is uitstekend, alsook de mogelijkheid tot het herconfigureren van de DMP. De MPU 6050 bevat een 3-assige accelerometer en een 3-assige gyroscoop. Via een I\textsuperscript{2}C is het mogelijk een externe magnetometer aan te sluiten. De data hiervan wordt opgenomen in de DMP bewerkingen.
						
						\item[MPU 9250:] Deze IMU beschikt over exact dezelfde mogelijkheden als de MPU 6050, maar heeft reeds een 3-assige magnetometer aan boord. Er dient dus geen externe magnetometer aangesloten te worden.

					\end{description}

				\par Er werd gekozen om de MPU9250 sensor te gebruiken bij het ontwerp van de quadcopter. Door de interne filter binnen de DMP wordt een Kalman filter overbodig in het FPGA ontwerp.

		\section{Serial peripheral interface}

			\par SPI is een veelgebruikt protocol voor communicatie tussen twee apparaten. Een SPI-bus bestaat uit vier signalen.

				\begin{description}

					\item[MOSI:] (Master Out Slave In) Dit signaal is de uitgang van de master en vormt de ingang van het slave apparaat. Via dit kanaal wordt informatie van de master naar de slave verstuurd.

					\item[MISO:] (Master In Slave Out) Dit signaal is de uitgang van de slave en vormt de ingang van het master apparaat. Via dit kanaal wordt informatie van de slave naar de master verstuurd.

					\item[SCLK:] (Serial Clock Line) Dit kanaal wordt gebruikt als klok. Het is het master apparaat dat de klok voorziet voor het slave apparaat. Data wordt enkel verstuurd en ontvangen als er een kloksignaal is.

					\item[SS:] (Slave Select) Via een slave select kan de master kiezen uit verschillende slave apparaten waarmee hij wil communiceren. Op deze manier kan een communicatie opgezet worden met meerdere apparaten door middel van \'e\'en master apparaat.

				\end{description}

			\par Zoals reeds eerder werd aangehaald, bestaat een SPI interface uit \'e\'en master apparaat en verschillende slave apparaten. Hierbij kan de master communiceren met elke slave, maar een slave kan enkel communiceren met de master. Aan de hand van een uniek slave select signaal voor elke slave wordt de selectie gemaakt. De communicatie gebeurt full duplex. 

			\par De vereiste voor de klok is dat zijn frequentie lager moet zijn dan de maximale frequentie van de betrokken toestellen. Binnen SPI zijn er twee parameters waarbij rekening gehouden moet worden.

				\begin{description}

					\item[CPOL:] De Clock polarity geeft aan wat de standaard waarde is van het kloksignaal wanneer de SPI-bus zich in de idle toestand bevindt. 

					\item[CPHA:] De Clock phase geeft aan op welke edge van het signaal gesampled zal worden. Een 0 geeft aan dat er op de rising edge gesampled wordt. Een 1 geeft aan dat er op de falling edge gesampled wordt.

				\end{description}

			\par Door het combineren van bovenstaande parameters kan men vier verschillende modi onderscheiden binnen de SPI interface. In figuur \ref{spi_clock} is een overzicht weergegeven van een SPI communicatie tussen twee apparaten. Hierbij zijn de CPOL en CPHA beide ingesteld op 0.

				\begin{figure}[H]					  
					  \centering
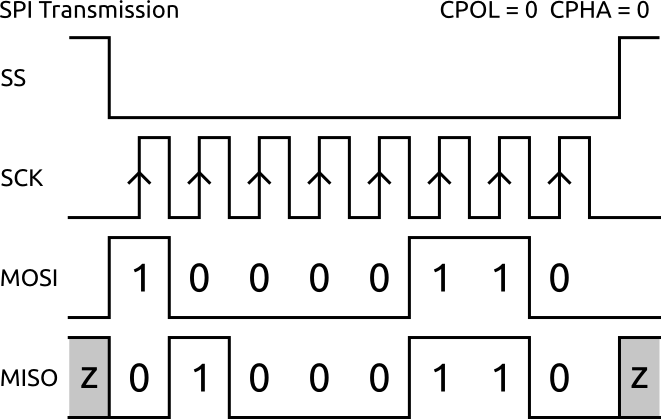
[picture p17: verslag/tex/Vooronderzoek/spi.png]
					  
					  \caption{Overzicht van SPI communicatie tussen master en slave}
					  \label{spi_clock}
				\end{figure}

			\par Op het moment dat de master een clock genereert, zal de communicatie aanvatten. Zowel de master als de slave zullen gelijktijdig data uitwisselen.  

			\par Wanneer de SS naar een lage toestand gebracht wordt, zal de slave geselecteerd worden. Vervolgens genereert de master het kloksignaal en start daarbij ook met versturen van data. Het slave apparaat zal ook starten met sturen van data op de wijzigende flanken van de klok. Wanneer de communciatie voltooid is, stopt de klok en wordt de SS weer naar hoge toestand gebracht.

			\par Om data van de slave op te vragen, moet dus eerst een bericht verzonden worden van welke data men wil opvragen. Daarna moet men nog een bericht versturen om de data te ontvangen. Dit is nodig aangezien het zenden en ontvangen steeds gelijktijdig gebeurt.
\newpage
		\section{Systeemoverzicht}

			\par De resultaten van dit vooronderzoek hebben geleid tot een systeem dat in staat is om de attitude van de quadcopter te controleren. Dit systeem dient in de volgende fase van het project ge\"implementeerd te worden in een FPGA. In figuur \ref{systeemoverzicht} is een overzicht van dit systeem weergegeven.

				\begin{figure}[H]					  
					  \centering
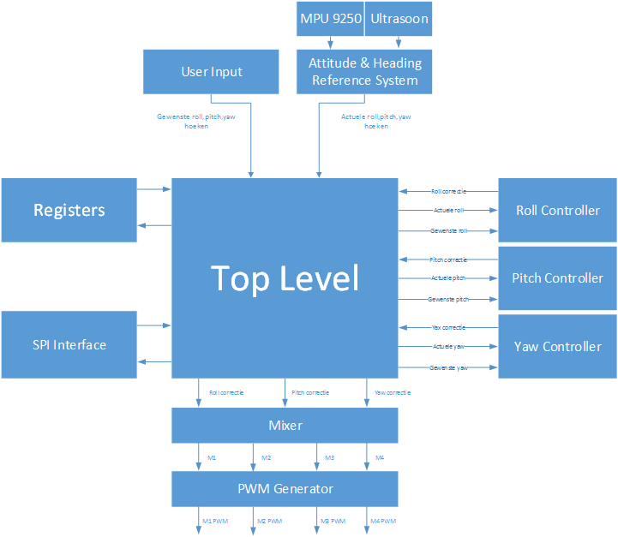
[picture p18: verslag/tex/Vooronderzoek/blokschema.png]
					  
					  \caption{Schematische voorstelling van de quadcopter autopilot}
					  \label{systeemoverzicht}
				\end{figure}
\newpage
			\par In de figuur kan men volgende blokken onderscheiden.

				\begin{description}

					\item[User input:] Deze blok is verantwoordelijk voor het afhandelen van de gebruikersinvoer. Deze is afkomstig van de RF antenne. Een PWM signaal per kanaal dient gelezen te worden. Dit PWM signaal wordt door het toplevel doorgegeven aan de PID controllers om zo de gewenste actie te ondernemen.

					\item[Registers:] In de registers worden alle verschillende instellingen bewaard. Naast deze instellingen worden ook waarden aangeboden aan de gebruiker. Via een SPI interface kan het register gelezen en beschreven worden.

					\item[SPI interface:] De SPI slave interface maakt het mogelijk om zowel te communiceren met een externe microcontroller als de MPU9250 die dienst doet als IMU uit te lezen.

					\item[Mixer:] De mixer is verantwoordelijk voor de verwerking van alle data die afkomstig is van de PID controllers voor rol, pitch en yaw. Aan de hand van deze informatie zal de mixer de geschikte PWM waarden berekenen voor de motoren. Hierbij zal rekening gehouden worden met de maxima en minima die ingesteld zijn in de registers.

					\item[PWM generator:]  De BLDC motoren worden aangestuurd door middel van een PWM signaal. De PWM generator zal voor elke motor een geschikt PWM signaal genereren op basis van de uitvoer van de mixer.

					\item[Roll controller:] De roll-controller stabiliseert het rollkanaal van de quadcopter. Naast de gebruikersinvoer vormt ook de roll-info van het AHRS een input voor deze controller.

					\item[Pitch controller:] De pitch-controller stabiliseert het pitchkanaal van de quadcopter. Naast de gebruikersinvoer vormt ook de pitch-info van het AHRS een input voor deze controller.

					\item[Yaw controller:]De yaw-controller stabiliseert het yawkanaal van de quadcopter. Naast de gebruikersinvoer vormt ook de yaw-info van het AHRS een input voor deze controller.

					\item[Attitude \& heading reference system:] Het AHRS geeft meer informatie over de attitude en heading van de quadcopter. Hiervoor gebruikt dit systeem verschillende sensoren. Dit AHRS systeem zal uitgevoerd worden op een aparte microcontroller en via een SPI interface waarden doorgeven aan het autopilot systeem.

				\end{description}

			\par In het volgende hoofdstuk zullen alle stappen besproken worden die nodig zijn om bovenstaande blokken te implementeren.

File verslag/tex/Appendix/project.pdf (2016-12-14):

% Work Complete
0%
Mon 23/02/15 Mon ‐ | 18/05/15
Name | Start | Finish | Work | Executor | Notes
Project management_2 | Mon 23/02/15 | Mon 18/05/15 | 338 hrs
Theoretische voorstudie | Tue 24/02/15 | Mon 2/03/15 | 28 hrs
Opzoekwerk Quadcopters | Tue 24/02/15 | Mon 2/03/15 | 5 hrs | Gert‐Jan | In dit deel van het vooronderzoek wordt een theoretische voorstudie gemaakt over quadcopter. Er wordt gekeken naar hoe deze bestuurd worden, welke technieken er bestaan en hoe men een goede stabiliteit kan bekomen....
Studie PID implementatie | Tue 24/02/15 | Mon 2/03/15 | 5 hrs | Gert‐Jan | In deze subtaak wordt een theoretische studie verricht naar hoe een PID regelaar kan geïmplementeerd worden op een FPGA. Hiernaast zal ook de algemene werking van een PID regalaar bestudeerd worden....
Kalman filter | Tue 24/02/15 | Mon 2/03/15 | 4 hrs | Gert‐Jan | In deze subtaak zal de Kalman filter van naderbij bekeken worden. Er zal onderzocht worden of het mogelijk is deze ook in de FPGA te integreren. Er wordt zowel gekeken naar footprint als haalbaarheid binnen het gegeven tijdsdomein. Ook de theorie achte...
Studie naar BLDC sturing | Tue 24/02/15 | Mon 2/03/15 | 3 hrs | Nick | Brushless DC motoren zijn betrouwbaar en licht, waardoor dit de optimale keuze is voor multicopters. De sturing hiervan is echter complexer dan brushed DC motoren. Hiervoor dient dus een stuurkring ontwikkeld te worden die de 4 motoren kan bedienen.
Optical Flow | Tue 24/02/15 | Mon 2/03/15 | 5 hrs | Nick | Er zijn reeds verschillende optical flow sensoren en kits beschikbaar. Het is de bedoeling een beste mogelijkheid te zoeken en deze te implementeren.
Mavlink protocol | Tue 24/02/15 | Mon 2/03/15 | 2 hrs | Nick | MAVlink is een communicatieprotocol dat geen fysische transportlaag gedefinieerd heeft. Het bevat enkel de data die moet overgedragen worden. Dit protocol moet dus geïmplementeerd worden op een zelf te selecteren fysische laag.

TASKS QUADCOPTER PROJECT
Overview of the upcomming task

# UPCOMING TASKS

Antenne design | Tue 24/02/15 | Mon 2/03/15 | 4 hrs | Nick | Voor de gekozen fysische laag voor het MAVlink protocol dient een correcte antenne ontworpen te worden. Hierbij spelen interefentie en antennelengte een grote rol.
FPGA Implementatie | Mon 23/02/15 | Mon 4/05/15 | 103 hrs | Gert‐Jan
Register implementatie | Mon 2/03/15 | Mon 27/04/15 | 33 hrs | Gert‐Jan
SPI Interface ‐ Externe communicatie | Mon 2/03/15 | Mon 9/03/15 | 5 hrs | Gert‐Jan | Om te communiceren met een externe microcontroller zal het SPI protocol gebruikt worden. Hiervoor is het noodzakelijk om een SPI controller te implementeren op de FPGA die het mogelijk maakt bepaalde registers in te stellen en uit te lezen. Ook de beri...
Register block ram | Mon 2/03/15 | Mon 9/03/15 | 3 hrs | Gert‐Jan | Het register block ram bevat alle instellingen van de FPGA autopilot. Deze registers kunnen gelezen en beschreven worden door verschillende componenten binnen de FPGA. In deze subtaak worden het register opgebouwd en voorzien van de nodige documentatie.
PID Regeling | Tue 10/03/15 | Mon 27/04/15 | 25 hrs | Gert‐Jan
PID Ontw erp | Tue 10/03/15 | Mon 23/03/15 | 15 hrs | Gert‐Jan | In deze subtaak wordt een PID regelaar ontwerpen op een FPGA. Deze regelaar ontvangt inputs van de MPU9250, Optical Flow en andere aangesloten sensoren. Eerst zal er een theoretisch model in Matlab gemaakt worden, waarna het geïmplementeerd wordt in VH...
P,I,D para mete rbepa ling | Mon 13/04/15 | Mon 27/04/15 | 10 hrs | Gert‐Jan | Het 'tunen' van de P, I, D parameters wordt aan het einde van het project vervolledigd. Hiervoor is het noodzakelijk dat alle systemen 'up and running' zijn. In dit process zullen de P,I en D parameters experimenteel bijgeregeld worden.
Uitlezen Sensoren | Mon 23/02/15 | Mon 30/03/15 | 30 hrs | Gert‐Jan
I2C interface | Mon 9/03/15 | Mon 16/03/15 | 10 hrs | Gert‐Jan | De sensoren die aangsloten zijn op de FPGA communiceren met de FPGA door middel van een I2C inteface. Alvorens communicatie mogelijk is, is het alvast nodig om een I2C driver te implementeren in de FPGA. Deze driver zal dienst doen als I2C (single) mas...
MPU9250 | Mon 16/03/15 | Mon 23/03/15 | 8 hrs | Gert‐Jan | De MPU6050 is de sensor bevat een 3‐assige gyroscoop, accelerometer en magnetometer. Hij is de belangrijkste sensor van de autopilot. Deze sensor zal uitgelezen worden door middel van de I2C interface. Hiervoor dienen verschillende instellingen gemaak...
Optical Flow | Mon 23/03/15 | Mon 30/03/15 | 5 hrs | Gert‐Jan | In deze subtaak worden de gegevens van de optical flow sensor binnengelezen dit zal afhankelijk van het beschikbare communicatieprotocol ofwel via SPA ofwel via I2C gebeuren. De ingelezen data zal mee opgenomen worden in de PID regelaar.
RF Ontvanger ‐ Sturing | Mon 23/02/15 | Mon 30/03/15 | 7 hrs | Gert‐Jan | In deze subtaak wordt de data voor de besturing van de quadcopter binnengelezen. Deze data is afkomstig van een externe micrcontroller die in contact staat met de grond. Communicatie kan gebeuren door middel van SPI of I2C.

Motor Mixing | Mon 20/04/15 | Mon 4/05/15 | 20 hrs | Gert‐Jan

PWM
Generatie
| Mon 20/04/15 | Mon 27/04/15 | 5 hrs | Gert‐Jan | Om de BLDC motoren aan te sturen is een PWM of PPM signaal nodig. Er werdt gekozen voor een PWM signaal. Hiervoor dient een interface aangemaakt te worden die het mogelijk maakt om deze PWM signalen te genereren.
Motor Mixing Algoritme | Mon 20/04/15 | Mon 4/05/15 | 15 hrs | Gert‐Jan | De motors van de quadcopter staan in voor zowel besturing als hoogte. Elk van de 4 motoren moet op een correcte manier aangestuurd worden om de gewenste attitude en altitude te verkrijgen. De uitvoer van de PID regelaar zal als invoer dienen voor het m...
Kalman filter implementatie | Mon 23/03/15 | Mon 27/04/15 | 20 hrs | | Het inlezen van sensoren brengt vaak veel ruis met zich mee waardoor de berekeningen (PID) gebeuren met niet correcte waarden. Om deze ruis deels weg te filteren zal getracht worden een Kalman filter te implementeren die het ruisgehalt in sensordate ee...
Quadcopter Frame | Tue 3/03/15 | Tue 5/05/15 | 56 hrs
Frame Design | Tue 3/03/15 | Tue 10/03/15 | 6 hrs | Gert‐Jan | Deze sub‐taak omvat het ontwerpen van een quadcopterframe dat geprint kan worden door middel van een 3D‐printer. Er dient dus rekening gehouden te worden met de maximale grootte van ieder onderdeel.
Frame Printing | Tue 10/03/15 | Tue 24/03/15 | 40 hrs | Gert‐Jan
Quadcopter assembly prototype | Tue 24/03/15 | Tue 31/03/15 | 6 hrs | Gert‐Jan & Nick
Quadcopter final assembly | Tue 28/04/15 | Tue 5/05/15 | 4 hrs | Gert‐Jan & Nick
Brushless DC sturing | Tue 24/02/15 | Mon 2/03/15 | 12 hrs | Nick
Hardware implemetatie | Tue 24/02/15 | Mon 2/03/15 | 8 hrs | Nick
Software implementatie | Tue 24/02/15 | Mon 2/03/15 | 4 hrs | Nick
Battery management | Tue 3/03/15 | Mon 9/03/15 | 14 hrs | Nick
Spanningsniveau detectie | Tue 3/03/15 | Mon 9/03/15 | 10 hrs | Nick | Het bijhouden van het batterijniveau is van belang voor de return home functionaliteit en de algemene betrouwbaarheid van de quadcopter. Het spanningsniveau staat in rechtstreeks verband met de nog resterende capaciteit van de batterij, door het spanni...
Controller overwrite (return home) | Tue 3/03/15 | Mon 9/03/15 | 4 hrs | Nick | Indien de batterijspanning onder een bepaald niveau daalt, dient de quadcopter terug te keren naar de home positie. Dit niveau is dynamisch te bepalen, en is afhankelijk van de nog te vliegen weg en het gemiddelde verbruikte vermogen. Zo kan er gegaran...

gemiddelde verbruikte vermogen. Zo kan er gegaran...

MAVlink protocol | Tue 10/03/15 | Mon 16/03/15 | 29 hrs | Nick
Physical link (RF‐WiFi‐ BT‐…) | Tue 10/03/15 | Mon 16/03/15 | 14 hrs | Nick | Het bepalen van het ideale fysische protocol is afhankelijk van verschillende factoren. De mogelijkheden zijn 433MHz, 2.4GHz, Bluetooth (2.4GHz) of WiFi (2.4GHz). Lagere frequenties hebben een kleiner verlies dan hogere frequenties over dezelfde afstan...
Antenna design | Tue 10/03/15 | Mon 16/03/15 | 10 hrs | Nick | Het bekijken en berekenen van het optimale antenne‐ontwerp voor deze specifieke toepassing. Dit kan een pcb‐antenne zijn, of een externe antenne. De keuze is afhankelijk van het gekozen protocol en kan dan ook pas na deze keuze bepaald worden.
Communicatie test | Tue 10/03/15 | Mon 16/03/15 | 5 hrs | Nick | Het testen van de communicatie met behulp van een simpele opstelling. Zenden en ontvangen kan getest worden met behulp van een opstelling van twee arduinos of mbeds om zo te controlleren dat het MAVlink protocol correct is geïmplementeerd.
Ontwerpen PCB | Tue 17/03/15 | Mon 30/03/15 | 36 hrs | Nick
PCB design | Tue 17/03/15 | Tue 24/03/15 | 30 hrs | Nick | Het tekenen van de PCB zelf, met alle nodige componenten aanwezig. Hierbij dient rekening gehouden te worden met EMC, door de aanwezigheid van hoogfrequente signalen afkomstig van de transceiver en de PWM signalen voor de motoren.
Controlleren schematic | Tue 24/03/15 | Mon 30/03/15 | 2 hrs | Nick
Controlleren board | Tue 24/03/15 | Mon 30/03/15 | 3 hrs | Nick
Genereren Gerber files | Mon 30/03/15 | Mon 30/03/15 | 1 hr | Nick | Het Gerber bestandsformaat is een universeel formaat dat gebruikt wordt bij de productie van PCB's. Om dus een correct geproduceerd bord te verkrijgen dienen deze bestanden te voldoen aan de eisen van de fabrikant.
Optical flow | Tue 31/03/15 | Mon 4/05/15 | 60 hrs | Nick
Image processing | Tue 31/03/15 | Mon 20/04/15 | 40 hrs | Nick | Image processing is nodig om de optical flow te detecteren. Drift cancellation maakt namelijk gebruik van de data die verkregen wordt uit het correleren van het huidige beeld met het vorige beeld. Op die manier kan berekend worden hoeveel drift de quad...
Return home | Mon 20/04/15 | Mon 4/05/15 | 20 hrs | Nick | De optical flow sensor kan ook ingeschakeld worden om te berekenen in welke mate de quadcopter beweegt. Hiervoor dient continu bijgehouden te worden in welke richting bewogen is in de x en y richting. Bewegingen in de z richting worden opgevangen door ...
Testing ‐ Debugging en Optimalisatie | Tue 5/05/15 | Mon 18/05/15 | 0 hrs | Gert‐Jan & Nick

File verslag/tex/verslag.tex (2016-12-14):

\documentclass[master=elt,masteroption=eo,oneside]{kulemt}
%\pagestyle{}
\usepackage{titlesec}

\setup{title={Ontwerp van een quadcoptersturing in VHDL },
  author={Andries Gert-Jan},
  promotor={Ing.\ Sammy~Verslype},
  assessor = {Ing.\ Sammy~Verslype},
  assistant={Ing.\ Sammy~Verslype}}

% De volgende \setup mag verwijderd worden als geen fiche gewenst is.
%\setup{filingcard,
%    translatedtitle={place english translation of title here}, 
%    udc=621.3,
%    shortabstract={Hier komt een heel bondig abstract van hooguit 500
%    woorden. \LaTeX\ commando's mogen hier gebruikt worden. Blanco lijnen
%    (of het commando \texttt{\string\pa r}) zijn wel niet toegelaten!
%    \endgraf \lipsum[2]}}
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
    \pgfmathsetmacro{\picxscale}{#1/\picwidth}
    \pgfmathsetmacro{\picyscale}{#2/\picheight}
    \xdef\xsca{\picxscale}
    \xdef\ysca{\picyscale}
}

\newcommand{\xyscaledtikz}[3]% draw commands, width, height
{ \smash{\vphantom{
    \begin{tikzpicture}
        #1
        \getsizes{#2}{#3}
    \end{tikzpicture}
    }}
    \begin{tikzpicture}[xscale=\xsca,yscale=\ysca]
        #1
    \end{tikzpicture}
}

\pgfplotsset{compat=1.8}

%%listings
\definecolor{mygreen}{rgb}{0,0.6,0}
\definecolor{mygray}{rgb}{0.5,0.5,0.5}
\definecolor{mymauve}{rgb}{0.58,0,0.82}
\definecolor{lightgray}{rgb}{.9,.9,.9}
%%tables
\definecolor{rulecolor}{RGB}{0,0,0}
\definecolor{tableheadcolor}{gray}{0.92}

%%commands
\newcommand{\topline}{ 
        \arrayrulecolor{rulecolor}\specialrule{0.1em}{\abovetopsep}{0pt}
        \arrayrulecolor{tableheadcolor}\specialrule{\belowrulesep}{0pt}{0pt}
        \arrayrulecolor{rulecolor}}

\newcommand{\midtopline}{ 
        \arrayrulecolor{tableheadcolor}\specialrule{\aboverulesep}{0pt}{0pt}
        \arrayrulecolor{rulecolor}\specialrule{\lightrulewidth}{0pt}{0pt}
        \arrayrulecolor{white}\specialrule{\belowrulesep}{0pt}{0pt}
        \arrayrulecolor{rulecolor}}

\newcommand{\bottomline}{ 
        \arrayrulecolor{white}\specialrule{\aboverulesep}{0pt}{0pt}
        \arrayrulecolor{rulecolor} 
        \specialrule{\heavyrulewidth}{0pt}{\belowbottomsep}}

\newcommand{\midheader}[2]{
        \midrule\topmidheader{#1}{#2}}

\newcommand\topmidheader[2]{\multicolumn{#1}{c}{\textsc{#2}}\\
                \addlinespace[0.5ex]}

\newcolumntype{C}{>{\raggedright\arraybackslash}p{7cm}}
\newcolumntype{D}{>{\raggedright\arraybackslash}p{3cm}}
\newcolumntype{A}{>{\raggedright\arraybackslash}p{2cm}}
\newcolumntype{B}{>{\raggedright\arraybackslash}p{4cm}}
\newcolumntype{F}{>{\raggedright\arraybackslash}p{0.20\textwidth}}
\newcolumntype{G}{>{\raggedright\arraybackslash}p{0.15\textwidth}}
\newcolumntype{I}{>{\raggedright\arraybackslash}p{0.25\textwidth}}
\newcolumntype{J}{>{\raggedright\arraybackslash}p{0.35\textwidth}}
\newcolumntype{K}{>{\raggedright\arraybackslash}p{0.45\textwidth}}

%%Tables
\pgfplotstableset{
        normal/.style ={
        header=true,
        string type,
        %font=\addfontfeature{Numbers={Monospaced}}\small,
        column type=l,
        every odd row/.style={
            before row=
        },
        every head row/.style={
            before row={\topline\rowcolor{tableheadcolor}},
            after row={\midtopline}
        },
        every last row/.style={
            after row=\bottomline
        },
        col sep=&,
        row sep=\\
    },
    center/.style ={
        header=true,
        string type,
        %font=\addfontfeature{Numbers={Monospaced}}\small,
        column type=c,
        every odd row/.style={
            before row=
        },
        every head row/.style={
            before row={\topline\rowcolor{tableheadcolor}},
            after row={\midtopline}
        },
        every last row/.style={
            after row=\bottomline
        },
        col sep=&,
        row sep=\\
    }
}

% monospaced font with bold variant

%%%%%%%%%%%%%%%%%%%%%%%%%%%%%%%%%%%%%%%%%%%%%%%%%%%%%%%%%%%%%%%%%%%%%%%%%%%%%%%

% Kies de fonts voor de gewone tekst, bv. Latin Modern
%\setup{font=lm} %T en nog een aantal andere letters zijn kleiner dan andere, dit trekt echt op niets in bvb 'NTC'. Zonder die instelling is er eensgezindheid onder de hoofdletters
\setlength{\parskip}{1em}
\setlength\parindent{0pt}

\titleformat{\chapter}[display]
    {\normalfont\huge\bfseries}{\chaptertitlename\ \thechapter}{20pt}{\Huge}
\titlespacing*{\chapter}{0pt}{-40pt}{10pt}

%%%%%%%
% Om wat tekst te genereren wordt hier het lipsum pakket gebruikt.
% Bij een echte masterproef heb je dit natuurlijk nooit nodig!
\IfFileExists{lipsum.sty}%
 {\usepackage{lipsum}\setlipsumdefault{11-13}}%
 {\newcommand{\lipsum}[1][11-13]{\par Hier komt wat tekst: lipsum ##1.\par}}
%%%%%%%

\begin{document}

%----------------------------------------------------------------------------------------------------------------------------------------------------
%\begin{preface}
%  \par Het tot stand komen van deze masterproef is het resultaat van een samenwerking tussen heel wat mensen. Van deze gelegenheid wensen wij gebruik te maken om alle personen te bedanken die rechtstreeks en onrechtstreeks bijgedragen hebben aan het tot stand komen van deze masterproef. 
%  \par Eerst en vooral willen wij alle docenten bedanken,  betrokken bij onze opleiding, meerbepaald de docenten van de afdeling electronica-ICT. In het bijzonder willen wij ook onze buitenpromotor, Crombez Pieter, bedanken voor de uitstekende begeleiding  van onze masterproef. Verder bedanken wij ook onze binnenpromotor Verslype Sammy en opleidingshoofd Peuteman Joan. Tot slot bedanken wij ook onze ouders en familie om ons de kans te geven deze opleiding te volgen. 
%\end{preface}
%----------------------------------------------------------------------------------------------------------------------------------------------------

\tableofcontents*

%-------------------------
\begin{abstract}
    \par In dit projectlab wordt een quadcoptersturing ontworpen op een FGPA. Aan de hand van een PID regeling wordt de stabilisatie voorzien rond de drie bewegingsassen van de quadcopter. Vanwege de beperkte hoeveelheid resources die op de FPGA aanwezig zijn, dient er in het hardware ontwerp rekening gehouden te worden met deze beperking. Verschillende iteraties en methodieken worden ondernomen om de benodigde resources voor deze PID regeling tot een minima te beperken. Zo werd onderzocht of er gebruik gemaakt kan worden van de snelle DSP48 slices. Daarnaast wordt ook een implementatie gemaakt aan de hand van de IP CoreGenerator multiplier. 

    \par Naast het ontwerpen van een PID controller worden ook verschillende andere systeemcomponenten ontworpen. Een PWM generator zal de BLDC motoren voorzien van een gepast PWM signaal dat voldoet aan de frequentievoorschriften van de motorfabrikant. Om het juiste signaal voor elke motor te genereren, wordt een motormixing unit ontworpen die het motormixingalgoritme implementeert. 

    \par Communicatie met de buitenwereld wordt voorzien door middel van een SPI slave interface. Deze interface wordt gebruikt om sensorwaarden te ontvangen, maar laat de gebruiker ook toe bepaalde registers uit te lezen of in te stellen.

    \par Alle hardware wordt gesimuleerd en vervolgens getest op een FPGA. Via Matlab en Simulink worden vooraf de nodige berekeningen en simulaties uitgevoerd die als basis voor het FPGA design dienen.

    \par Naast de hardware wordt ook het quadcopterframe volledig ontworpen. Dit frame wordt zodanig ontworpen dat het uit verschillende onderdelen bestaat die door een 3D printer vervaardigd kunnen worden.
\end{abstract}
%-------------------------

%include the symbols and abbreviations list from different file to keep it all organized
\include{SymbolsAbbs/SymbolsAndAbbreviations}

% Nu begint de eigenlijke tekst
\mainmatter

\include{Inleiding/Inleiding}
\include{Vooronderzoek/Vooronderzoek}
\include{Implementatie/Implementatie}
%\include{Chapter_3/hfdst-3}
%\include{Chapter_4/hfdst-4}
%\include{Chapter_5/vooronderzoek}
\include{Besluit/besluit}

% Indien er bijlagen zijn:
\appendixpage*          % indien gewenst
\appendix
\include{Appendix/app-A}
% ... en zo verder tot
%\include{Appendix/app-n}

\backmatter
% Na de bijlagen plaatst men nog de bibliografie.
% Je kan de  standaard "abbrv" bibliografiestijl vervangen door een andere.
%\bibliographystyle{abbrv}
%\bibliography{referenties}

\end{document}

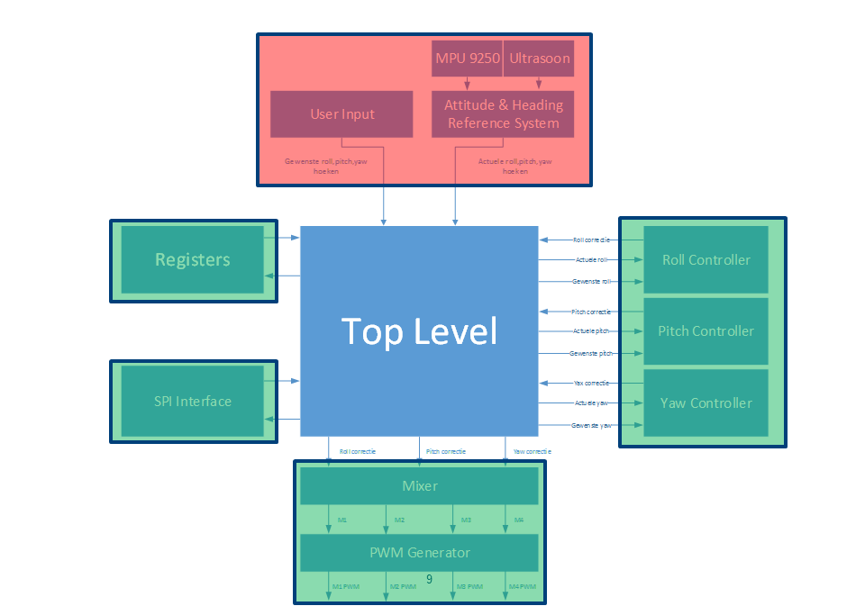
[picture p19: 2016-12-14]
pictures/architecture_overview.PNG

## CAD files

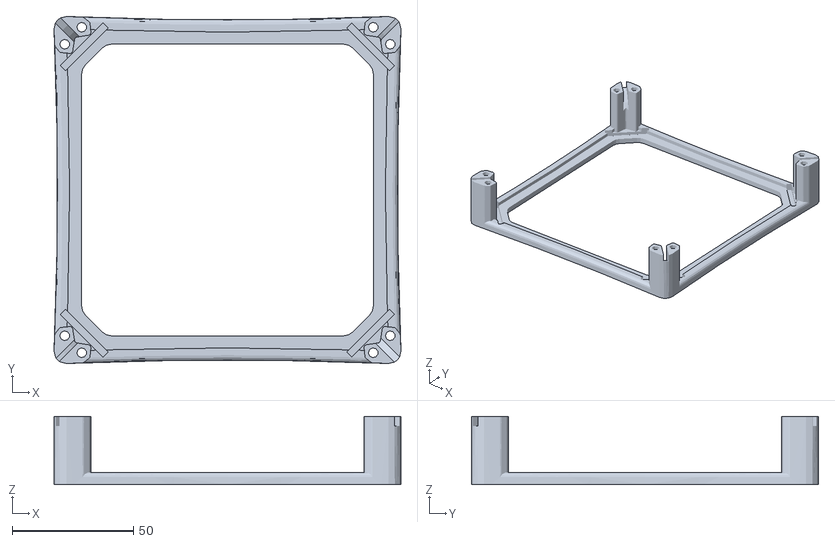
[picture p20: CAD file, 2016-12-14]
frame/FrameBody.stl
142.8 x 142.8 x 28.0

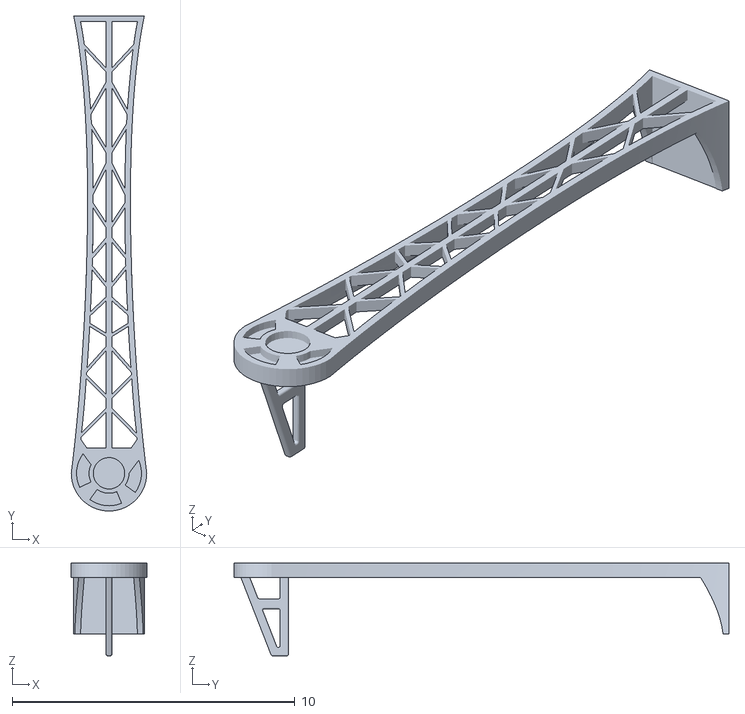
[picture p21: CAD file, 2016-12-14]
frame/FrameArm.stl
2.67 x 17.5 x 3.27

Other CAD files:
frame/Frame.ipt

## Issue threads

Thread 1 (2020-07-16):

problem simulating pwm_counter

charlicruz, 2020-07-16:
I am trying to simulate the pwm_counter and I use pwm_in as pwm_clock but I do not obtain any value form the output pwm_count. Do I need to have any stimulus in the testbench? I would like to check your code. Thank you in advance

 -- Stimulus process
   stim_proc: process
   begin
      -- hold reset state for 100 ns.
      wait for 100 ns;

      wait for CLK_period*10;
     wait;
   end process;
